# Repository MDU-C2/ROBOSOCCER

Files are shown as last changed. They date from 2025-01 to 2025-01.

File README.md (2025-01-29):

Multi-robot Soccer - RoboCup
=======================

About
-----------------------
Welcome to the DVA490 and DVA474 Project Course, project name Multi-robot Soccer - RoboCup. 
The project is about creating SSL RoboCup (Division B) robots and developing the accompanying software.

Roadmap
-----------------------
Hardware:
- [ ] Hardware mechanical design
- [ ] Hardware 3D design
- [ ] Hardware circuit/electrical design

Software:
- [x] Simulation Interface
- [x] SSL Interface
- [ ] Hardware Interface
- [ ] Communication protocol
- [ ] Raspberry Pi executable (Individual Robot Behaviour)
- [ ] Central computer executable (Collective Robot Behaviour)

Contributors and roles
-----------------------
This project was developed by:
- Mudar Ibrahim: Team leader and software developer
- Carl Larsson: Software lead and software developer
- Viktor Eriksson: Software developer
- Jacob Johansson: Software developer
- Aaiza Aziz Khan: Software developer
- Shruthi Puthiya Kunnon: Software developer
- Emil Åberg: Software developer
- Pontus Svensson: Hardware lead, hardware developer and software developer
- Anton Grusell: Hardware developer
- Johanna Melander: Hardware developer
- Fredrik Westerbom: Hardware developer and software developer

### Contact:
Carl Larsson: cln20001@student.mdu.se

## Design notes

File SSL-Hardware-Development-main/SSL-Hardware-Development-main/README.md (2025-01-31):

# SSL-Hardware-Development

## Overview
Welcome to the SSL Robot Project repository! This project encompasses both hardware and software components essential for building and controlling an SSL robot. Our goal is to create a robust, scalable, and maintainable robot platform.

## Repository Structure
- **3D_Models**: Contains all 3D models related to the robot design.
- **Circuits**: Circuit designs for various robot components.
- **BOM**: Bill of Materials for each component.
- **Software**: Firmware and software for motor control and other functionalities.
- **Design_Documents**: Technical specifications and design decisions.
- **Meeting_Notes**: Documentation of project meetings.
- **Misc**: Miscellaneous files and references.
- **Simulations**: Simulation scripts and models.
- **Documentation**: Comprehensive project documentation and guides.

```bash
/SSL-Robot-Project
├── /3D_Models
│   ├── /CAD_Files            # All CAD files for different robot parts
│   ├── /STL_Files            # STL exports for 3D printing
│   └── /Renderings           # Renders of the 3D models
├── /Circuits
│   ├── /Motor_Control        # Motor circuit design files
│   ├── /Kicker               # Kicker circuit design files
│   ├── /Dribbler             # Dribbler circuit design files
│   └── /Sensor               # Sensor circuit design files
├── /BOM                      # Bill of Materials for different components
├── /Software
│   ├── /Motor_Control
│   │   ├── /Firmware          # Firmware code for motor controllers
│   │   │   ├── /src           # Source code files
│   │   │   ├── /include       # Header files
│   │   │   ├── /tests         # Unit and integration tests
│   │   │   └── README.md      # Firmware-specific documentation
│   │   ├── /Software_Doc      # Documentation related to motor control software
│   │   │   ├── /API_Docs      # API documentation if applicable
│   │   │   └── /User_Guides   # User manuals or setup guides
│   │   ├── /Libraries         # Any libraries or dependencies specific to motor control
│   │   └── /Examples          # Example projects or usage scenarios
│   ├── /Kicker_Control        # Similar structure for kicker control software
│   ├── /Dribbler_Control      # Similar structure for dribbler control software
│   └── /Sensor_Control        # Similar structure for sensor control software
├── /Design_Documents          # Technical specifications, design decisions
├── /Meeting_Notes             # Notes from each project meeting
├── /Misc                      # Any other miscellaneous files
├── /Simulations               # Simulation files or scripts if applicable
├── /Documentation             # General documentation for the project
│   ├── README.md              # Overview of the project
│   ├── CONTRIBUTING.md        # Guidelines for contributing
│   ├── LICENSE.md             # Licensing information
│   └── /Wiki_Links            # Links to relevant wiki pages
└── .gitignore                 # Git ignore file
```

## Getting Started

### Prerequisites
- **Hardware**: Access to the necessary hardware components as listed in the BOM.
- **Software**: Install required software dependencies (refer to [Dependencies](Software/Software_Dependencies.md) documentation).

### Setup Instructions
1. **Clone the Repository**
    ```bash
    git clone git@github.com:DVA490-474-Project-Course/SSL-Hardware-Development.git
    cd SSL-Robot-Project
    ```

2. **Setup Software Environment**
    - Navigate to the software directory:
        ```bash
        cd Software/Motor_Control
        ```
    - Follow the instructions in `README.md` to build and deploy the firmware.

3. **Accessing Documentation**
    - Visit the [Wiki](https://github.com/DVA490-474-Project-Course/SSL-Hardware-Development/wiki) for detailed guides and API documentation.

## Contributing
We welcome contributions! Please read our [CONTRIBUTING.md](Documentation/CONTRIBUTING.md) for guidelines on how to get involved.

## License
This project is licensed under the [MIT License](Documentation/LICENSE).

## Contact
For any questions or support, please open an issue or contact the project maintainers.

Pontus Svensson - psn19003@student.mdu.se

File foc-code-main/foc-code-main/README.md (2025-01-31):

Field Oriented control (FOC)
=======================

DISCLAIMER
-----------------------
This code is DEPRICATED. It is incomplete and its only purpose is for future development.

When using the software provided by STM which supports their MCUs a lot of functions and libraries are generated. We have not been able to exclude the libraries generated that isn't necessary for the code to run. In this repo, the team have elected to only upload the main.c file which is the only file that has been changed by the developers. Later in this **README** there is a step-by-step instruction on what the team did in respective software so that those could generate the files. However, there is no way the team could ensure that even though a future user follows the steps provided in the **README** will generate the same files due to the fact that STM might not support the version the team have used in the future, or if STM elects to generate another code using a different library.

About
-----------------------
This repository contains the code running on the ESC for controlling the wheel motors using FOC.

## Built with
The following tools were used to generate and modify the code for FOC:
- [STM32CubeIDE 1.16.1](https://www.st.com/en/development-tools/stm32cubeide.html)
- [STM32CubeMX 6.12.1](https://www.st.com/en/development-tools/stm32cubemx.html)
- [MC Workbench 6](https://wiki.st.com/stm32mcu/wiki/STM32MotorControl:STM32_MC_Workbench) (Only available for Windows.)

Getting started
-----------------------

### Prerequisites

To retrace the steps the students made during the autumn semester of 2024 the hardware componentes below you will need in addtion to the software listed above. Also, you will need a power source and cables which you can solder onto the inverter and motor.

### Hardware
1. [Nanotec DF45L024048-A](https://www.nanotec.com/eu/en/products/1786-df45l024048-a)
2. [Electronic Speed Controller Discovery kit for drones with STM32G431CB B-G431B-ESC1](https://www.mouser.se/ProductDetail/511-B-G431B-ESC1)

### Installation
1. Clone the repository:
```
git clone https://github.com/DVA490-474-Project-Course/foc_code.git
```
2. Download and install STM32CubeIDE 1.16.1, STM32CubeMX 6.12, STM32 Motor Control Software Development Kit (please see ## Built with)

### Step-by-step configuration
1. In the MC Workbench, create a new project.
    1. Under 'General Info' select
        1. Project name 
        2. Num. Motors: 1 Motor
        3. Driving Algorithm: FOC
        4. Inverter
        5. Please see the image for a visual explanation
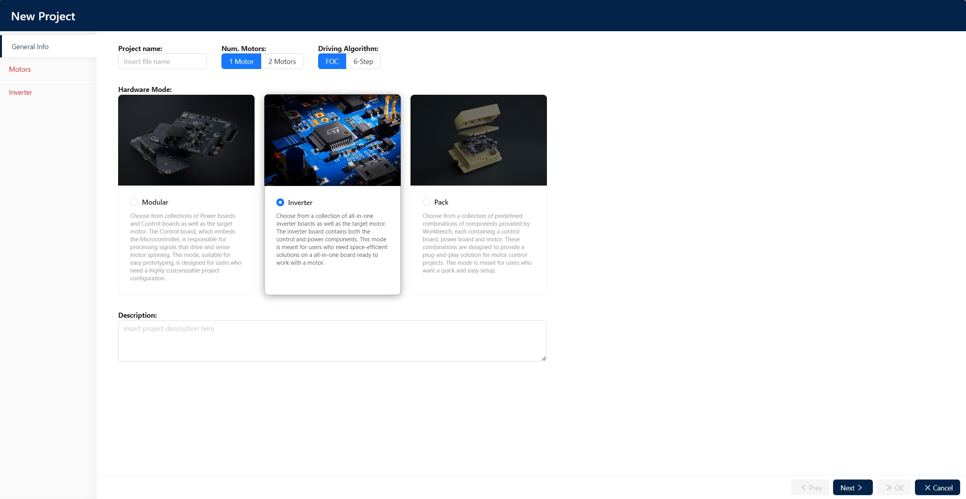
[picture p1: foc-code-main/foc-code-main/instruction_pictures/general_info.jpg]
General Info
        6. 

    2. Under *Motors* select a motor that is similar to the Nanotec DF45L024048-A
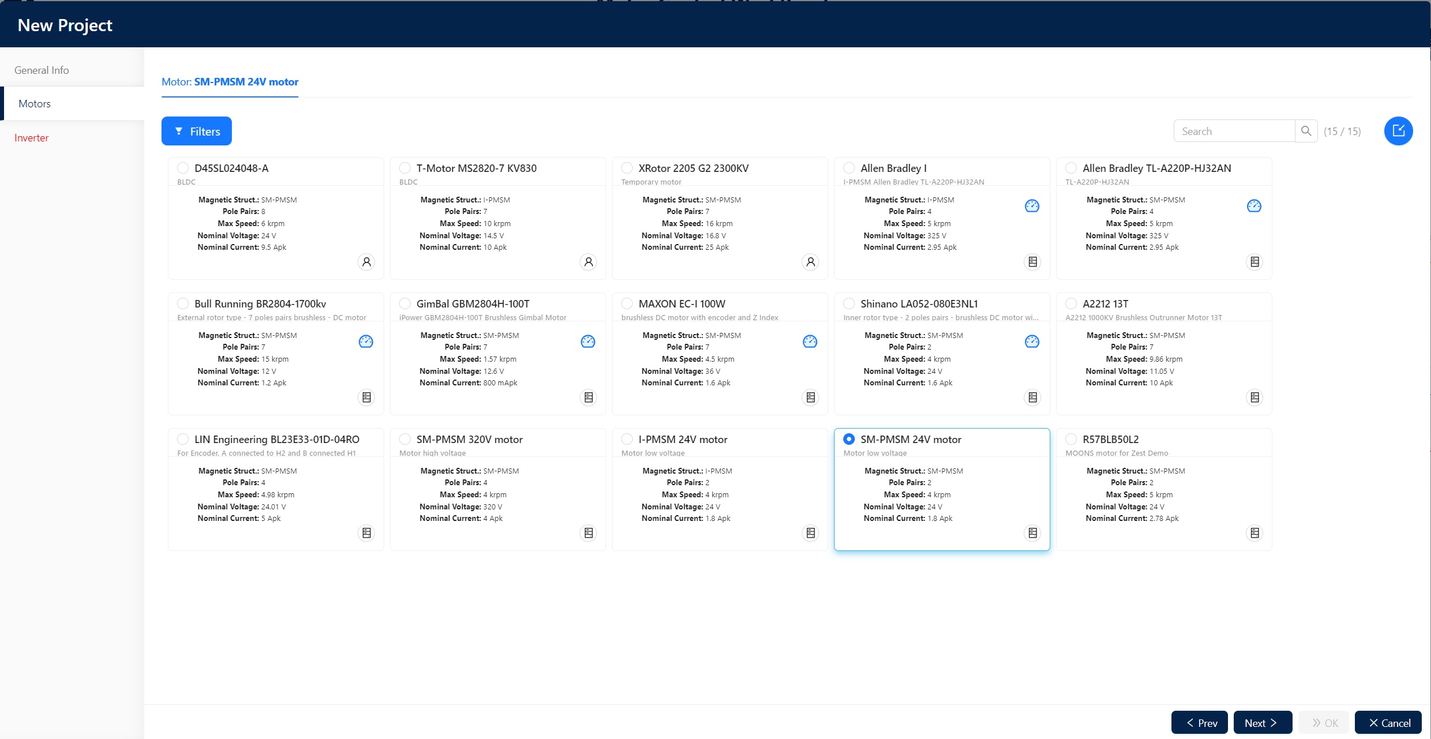
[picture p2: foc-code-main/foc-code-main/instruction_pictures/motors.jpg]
Motors
        1. 
    4. Under the *Inverter* tab select B-G431B-ESC1
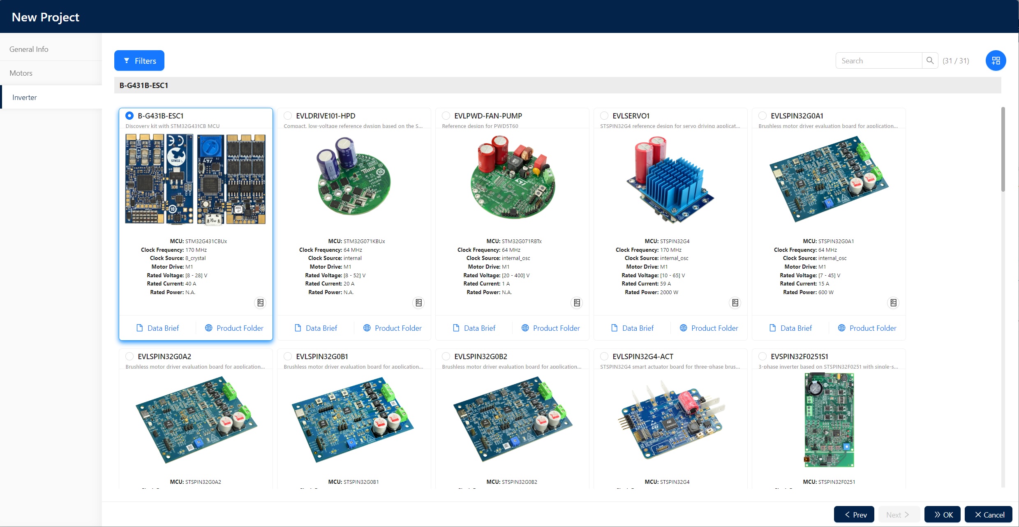
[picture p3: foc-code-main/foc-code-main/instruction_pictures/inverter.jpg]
Inverter
        1. 
    5. Once you've completed all the steps above click ok
2. In the next window called *Project Steps* select the *Application Configuration* tab, check the box for 'Motor Profiler' and click ok
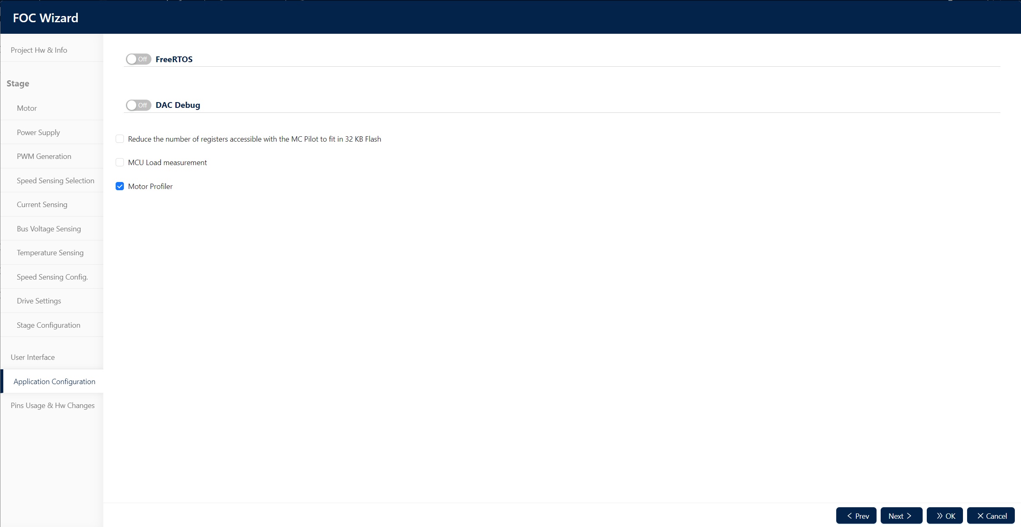
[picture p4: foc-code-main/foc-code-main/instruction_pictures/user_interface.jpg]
Application Configuration
    1. 
3. Click Generate the project - you will be asked to save the project as well.
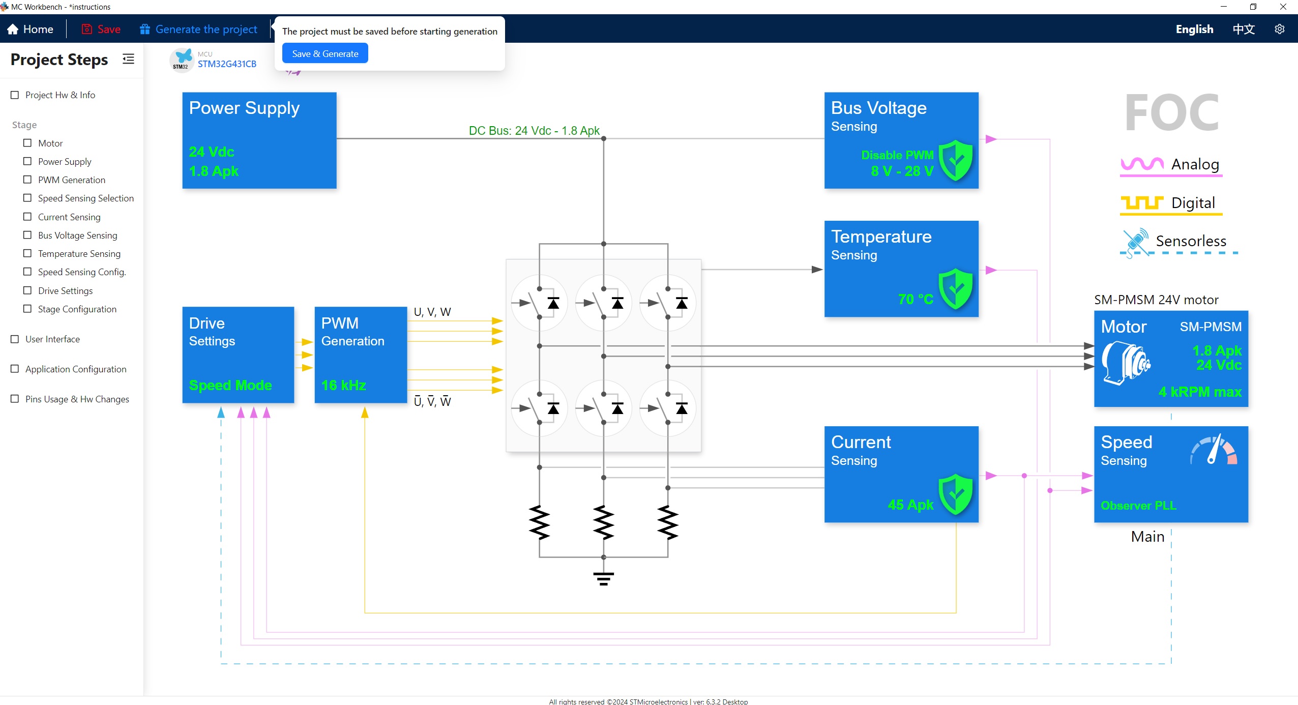
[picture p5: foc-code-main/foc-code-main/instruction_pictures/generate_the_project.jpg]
Generate the project
    1. 
4. A pop-up window will emerge, make sure that all the settings are the same as in the image below (in the extent that it is possible).
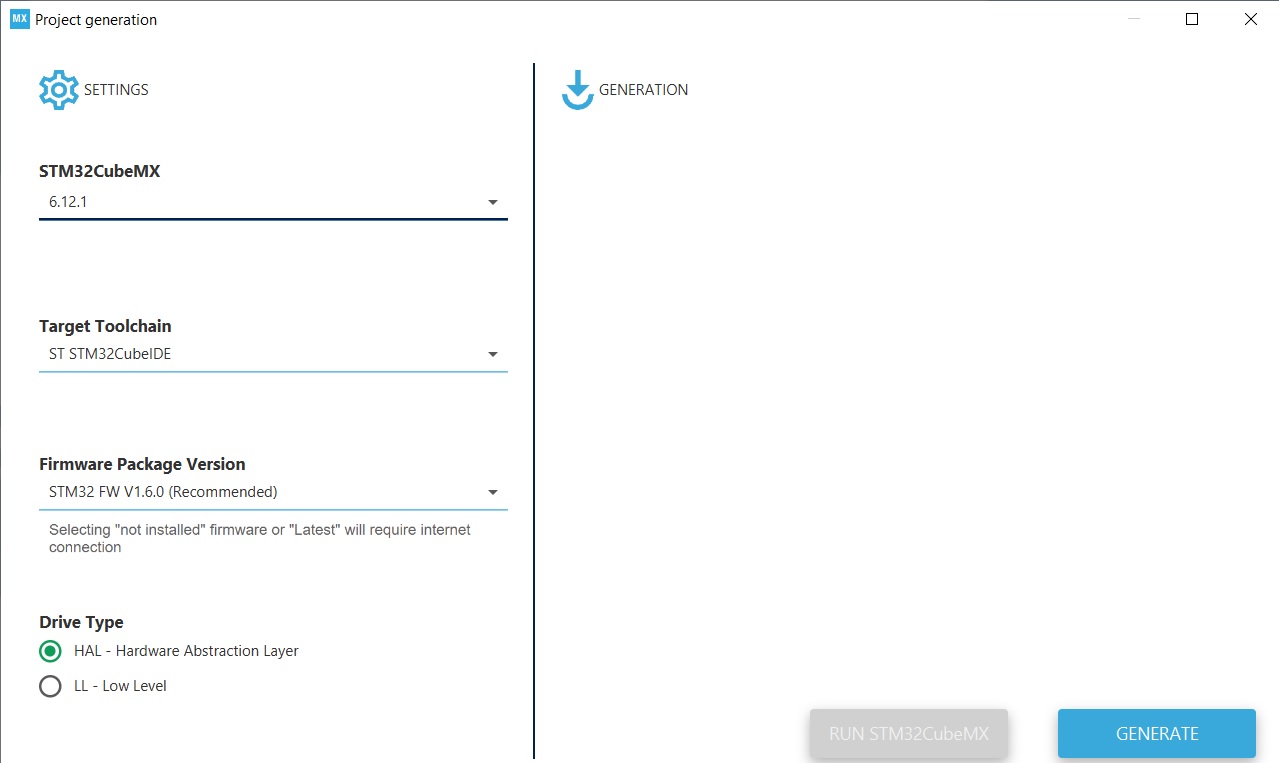
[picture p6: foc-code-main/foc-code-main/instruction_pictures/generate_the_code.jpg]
Generate the code
    1. 
    2. Once it has completed click 'RUN STM32CubeMX'
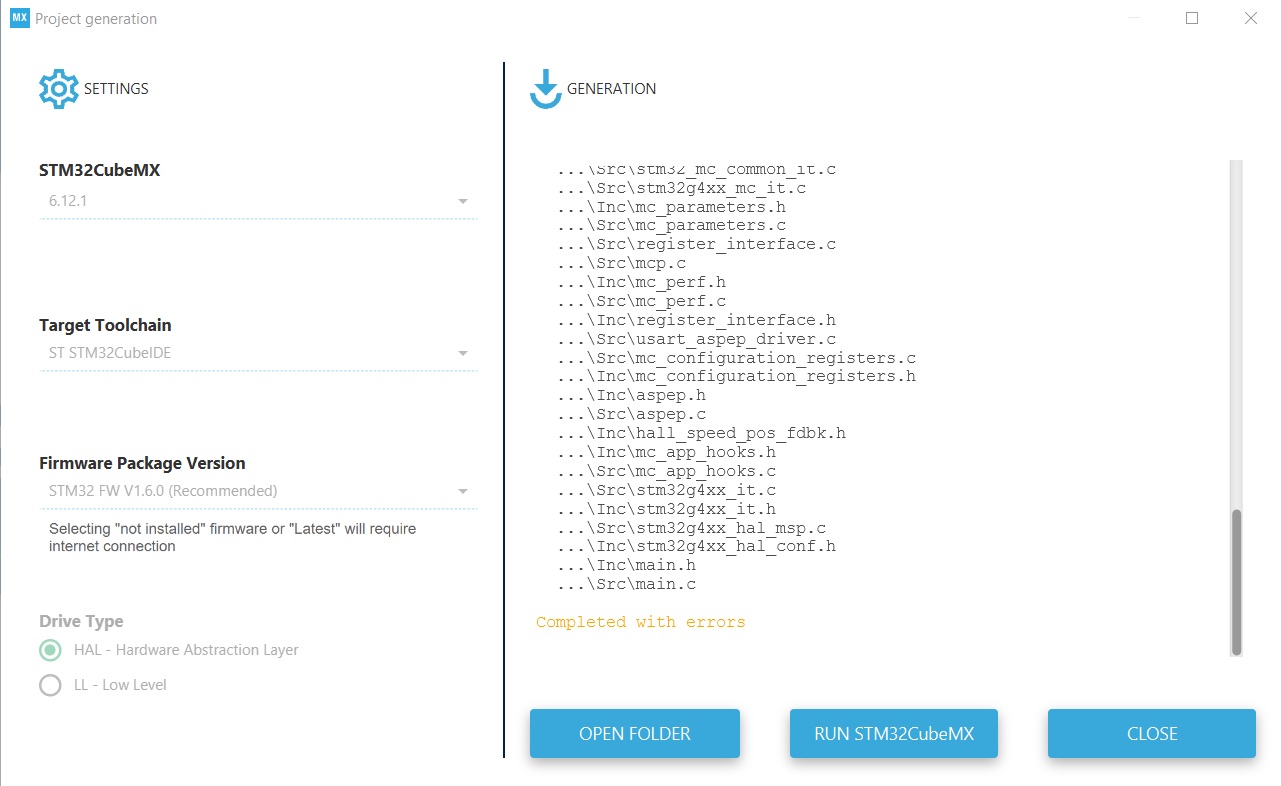
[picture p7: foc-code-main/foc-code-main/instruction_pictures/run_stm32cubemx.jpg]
RUN STM32CubeMX
    3. 
5. Once STM32CubeMX has launched go to the 'Pinout & Configuration' tab and select connectivity. Make sure that the settings for USART2 are the same as in the picture below.
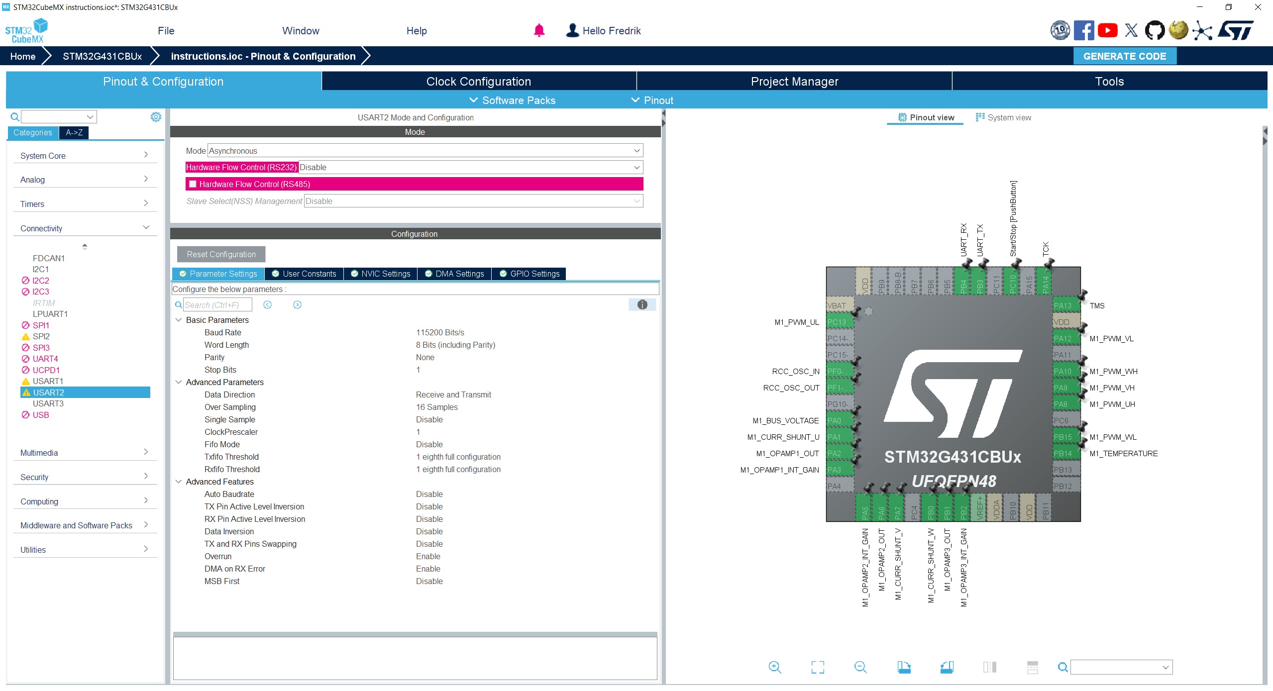
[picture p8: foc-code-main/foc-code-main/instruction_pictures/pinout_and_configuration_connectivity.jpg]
Pinout & Configuration - Connectivity
    1. 
6. Go to 'Project Manager' and in the first tab 'Project' make sure that the option 'Toolchain / IDE' is set to STM32CubeIDE, as seen in the picture (and highlighted with a red arrow).
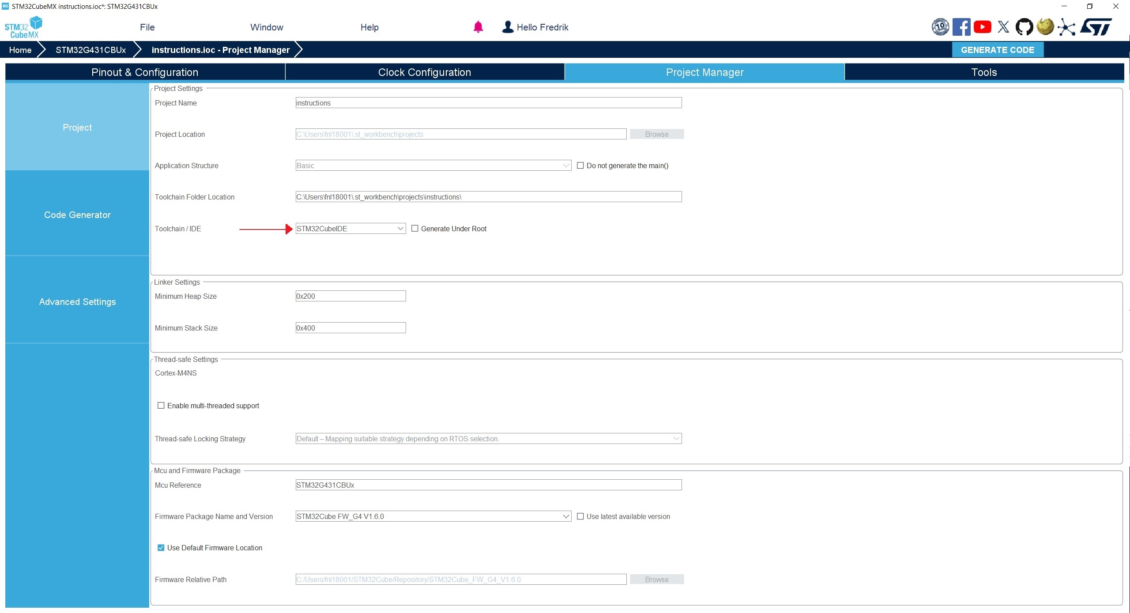
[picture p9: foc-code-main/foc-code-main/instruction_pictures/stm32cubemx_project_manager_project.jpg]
Project Manager - Project
    1. 

-----------------------

Roadmap
-----------------------
- [ ] Establish a connection using UART
- [x] Develop FOC

Design diagrams
-----------------------
Design diagrams/files can be found in the [docs](/docs) directory. Additionally 
they are available on:
- [Hardware Interface](https://www.mermaidchart.com/raw/11c442f5-192c-4ac3-b61e-867a3e2ca6ea?theme=dark&version=v0.1&format=svg)

License
-----------------------
A majority of the code is generated by the STM32CubeIDE and thus distributed under their License (see [liscense](/liscense.pdf)).

Contributors and contact
-----------------------
- Carl Larsson: cln20001@student.mdu.se
- Fredrik Westerbom

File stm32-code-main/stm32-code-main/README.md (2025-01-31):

About
-----------------------
This repository contains the executable code intended to run on the STM32H7 Nucleo-144 board.

### Built with
The stm32-code project is built with the following:

- [STM32CubeIDE](https://www.st.com/en/development-tools/stm32cubeide.html)
- [MicroRos](https://micro.ros.org/)
- [Docker](https://www.docker.com/)

Getting started
-----------------------

### Prerequisites

For STM32CubeIDE installation see: https://www.st.com/en/development-tools/stm32cubeide.html

On Ubuntu and other Debian derivatives, Docker can be installed with:
```
sudo apt install docker
```

In order for microRos dependencies to be downloaded when building, Docker must be
configured to run with root privilige. This can be done with:
```
sudo groupadd docker
sudo usermod -aG docker $USER
```

Log in and out after completing this step in order for group membership to be evaluated.

### Installation
1. Clone the repository and initialize the microROS submodule:
```
git clone https://github.com/DVA490-474-Project-Course/stm32-code.git
cd stm32-code
git submodule update --init --recursive
```
2. Start STM32CubeIDE

3. Log in to your ST account in the IDE if you aren't already logged on.

4. Click 'File>Open Projects from file System...'

5. Click the 'Directory...' button and select the repository folder.

6. Make sure the project is selected in the checklist and click 'Finish'.

7. Generate code by clicking 'Project>Generate Code'. The project is now ready to build.

Usage
-----------------------

In order to upload the program, connect the PC to the USB port CN1  (the one located on
the side of the board which contains the smaller processor, which is the debugger) and
click Run>Run.

Building for the first time may take a few minutes since microROS is downloading its
dependencies to the project.

Roadmap
-----------------------

- [x] Develop Sensor Interface
- [ ] Develop Kicker Interface
- [ ] Develop API to communicate with STM32 on wheel motors
- [ ] Develop API to communicate with STM32 on dribbler
- [x] Implement MicroROS Publishers
- [ ] Implement MicroROS Subscribers

Design diagrams
-----------------------

Design diagrams/files can be found in the [docs](/docs) directory. Additionally
they are available on:
- [Hardware Interface](https://www.mermaidchart.com/raw/11c442f5-192c-4ac3-b61e-867a3e2ca6ea?theme=dark&version=v0.1&format=svg)

License
-----------------------

This repository contains source files from third parties which are distributed
under the license conditions of the respective distrubutors. Source files
developed by the authors of this repository are located in the Core/Src/user-code
directory and is distrubted under the MIT Liscence.

See [MIT Licence](/Core/Src/user-code/LICENSE) for the MIT license.
See [STM32IDE License](/license.pdf) for licence conditions pertaining files accossiated with STM32IDE.
See [VL6180X Driver License](/Drivers/Adafruit_VL6180X/license.txt) for licence conditions pertaining Adafruit's VL6180X driver.
See [VL53L4CD Driver License](/Drivers/VL53L4CD_ULD_Driver/license.pdf) for licence conditions pertaining ST's VL53L4CD driver.
See [WSEN_ISDS Driver License](/Drivers/WSEN_ISDS_2536030320001/license_terms_wsen_sdk.pdf) for licence conditions pertaining Würth Elektronik's WSEN_ISDS driver.

Contributors and contact
-----------------------
- Aaiza Aziz Khan: akn23018@student.mdu.se
- Mudar Ibrahim: mim20004@student.mdu.se
- Shruthi Puthiya Kunnon: spn23001@student.mdu.se
- Emil Åberg: eag24002@student.mdu.se

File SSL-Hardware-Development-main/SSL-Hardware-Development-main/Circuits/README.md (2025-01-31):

# Circuit Designs

This folder contains all circuitry and PCB design for the robot.

See [CONTRIBUTING.md](Documentation/CONTRIBUTING.md#Contributing-to-Hardware) 

## Changes
Update your changes here, include a description, file, name and commit number.

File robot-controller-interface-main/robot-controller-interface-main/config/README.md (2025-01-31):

nav2 custom config files (DEPRICATED)
=======================
This part of the code, meaning setting up a custom nav2 stack and the 
associated config files, is depricated (and does not work). DO NOT USE IT, 
its only purpose is for future development.

The current issue is described in [this Robotics Stack Exchange Question](https://robotics.stackexchange.com/questions/113468/no-map-received-timed-out-waiting-for-transform-from-base-footprint-to-map).

Alternative
=======================
The temporary alternative is to use the default nav2 stack together with SLAM 
Toolbox. To start everything which is necessary to run the individual robot 
behaviour (path planning):
Start SLAM Toolbox (this requires publishing LIDAR values on the /scan topic):
```
ros2 launch slam_toolbox online_async_launch.py
```
Start the nav2 stack (This requires SLAM Toolbox and odometry being published 
on /odom topic):
```
ros2 launch nav2_bringup navigation_launch.py
```

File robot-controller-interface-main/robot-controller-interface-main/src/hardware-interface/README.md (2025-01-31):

Raspberry Pi to STM32 communication code (DEPRICATED)
=======================
This part of the code, meaning the code for Raspberry Pi to STM32 communication 
is in early development, and is depricated. DO NOT USE IT, 
its only purpose is for future development. Hence it has no documentation.

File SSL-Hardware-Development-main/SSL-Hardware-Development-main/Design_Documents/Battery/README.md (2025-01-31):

# What other teams have used
| battery | power board | Links | Team | Weight |
| --- | --- | --- | --- | --- |
| 6S1P 22.2V 150C LiPo 1300 mAh | custom powerboard | [TIGERS Mannheim 2020 paper](https://tdpsearch.com/#/tdp/soccer_smallsize__2020__TIGERs_Mannheim__0?ref=list) | TIGERs Mannheim | ~216 g  |
| 6S1P 22.2V LiPo | custom powerboard | [Roboteam Twente 2022 paper](https://tdpsearch.com/#/tdp/soccer_smallsize__2022__RoboTeam_Twente__0?ref=list) | Roboteam Twente | ~216 g  |
| Li-Po battery, 22.2 V nominal (6S1P), 1300 mAh | not specified | [RoboIME 2024 Paper](https://tdpsearch.com/#/tdp/soccer_smallsize__2024__RoboIME__0?ref=list) | RoboIME | ~240 g  |
| Li-ion,14.8V 4s1p,2600mAh | not specified | [Compilation Error 2024 paper](https://tdpsearch.com/#/tdp/soccer_smallsize__2024__Compilation_Error__0?ref=list) | Compilation error | ~190 g  |
| YPG 22.2V 1500mAh 70C | not specified | [Sysmic Robotics 2020 paper](https://tdpsearch.com/#/tdp/soccer_smallsize__2020__Sysmic_Robotics__0?ref=list) | Sysmic Robotics | ~350 g  |
| LiPo Battery 4S | Custom powerboard | [ITandroids 2020 paper](https://tdpsearch.com/#/tdp/soccer_smallsize__2020__ITAndroids__0?ref=list) | ITandroids | ~565 g  |

As there are no links to the given batteries, the weights are based on similar products found on google.

# requirements
- Correct voltage for processing unit, sensors,  maneuvering motors, dribbling motor and the kicker solenoid.
- The batteries should last for at least 15 minutes of continuous play.
- easy to replace.
- safe to handle.
- Lightweight.
- Correct C rating.

# Limitations
- Size
- Weight
- Capacity

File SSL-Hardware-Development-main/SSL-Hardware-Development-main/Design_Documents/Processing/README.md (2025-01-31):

## Candidates
- [Arduino Due](https://store.arduino.cc/products/arduino-due)
    - Expensive
    - Easy to program
    - No RF

- [STM32 Nucleo](https://estore.st.com/en/products/evaluation-tools/product-evaluation-tools/mcu-mpu-eval-tools/stm32-mcu-mpu-eval-tools/stm32-nucleo-boards/nucleo-f446ze.html)
    - Is a development board, might not have all necessary inputs
    - Cheap

- [Olimex](https://www.olimex.com/Products/ARM/ST/STM32-E407/open-source-hardware)
    - Cheap, supports a lot of communication protocols
    - Open source, a lot of documentation
    - Zephyr build system
    - [ZigBee RF module](https://www.olimex.com/Products/Modules/RF/)

- [STM32L4 Discovery kit IoT](https://estore.st.com/en/products/evaluation-tools/product-evaluation-tools/mcu-mpu-eval-tools/stm32-mcu-mpu-eval-tools/stm32-discovery-kits/b-l475e-iot01a.html)
    - Supports low power RF

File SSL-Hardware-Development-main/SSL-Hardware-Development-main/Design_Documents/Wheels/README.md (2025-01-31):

## Wheels from Participants 2024
- In all the papers reviewed from 2024, 4 omni wheels are consistently used. 
- 3D-printed wheels made from PLA did not hold up. 
- The wheel size depends on the weight of the robot. 
- Bigger wheels can make the robot faster, but the extra weight slows it down by requiring more energy to move.
- More rollers resulted in a smoother motion and more contact with the ground. 
## Team that switched from 3 to 4 wheels
- Some teams initially used 3 wheels but later switched to 4, without giving a specific reason for the change.

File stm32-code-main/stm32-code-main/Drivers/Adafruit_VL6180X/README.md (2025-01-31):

# Adafruit VL6180X Library Documentation

This is a library for the Adafruit VL6180X Time of Flight Distance Ranging Sensor:
  * https://www.adafruit.com/products/3316
 
Check out the links above for our tutorials and wiring diagrams. This chip uses I2C to communicate

Adafruit invests time and resources providing this open source code, please support Adafruit and open-source hardware by purchasing products from Adafruit!

Written by ladyada for Adafruit Industries. BSD license, all text above must be included in any redistribution

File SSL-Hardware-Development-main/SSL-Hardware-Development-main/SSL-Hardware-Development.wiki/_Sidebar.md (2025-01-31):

<!--TODO: Add functional requirements, robot specifications
Add the rest of the components
If the home page gets to long, consider dividing it into their own files and link to them -->
## [Home](https://github.com/DVA490-474-Project-Course/SSL-Hardware-Development/wiki)
## Introduction
- [Requirements](https://github.com/DVA490-474-Project-Course/SSL-Hardware-Development/wiki/Requirements)
- [Functional Requirements](https://github.com/DVA490-474-Project-Course/SSL-Hardware-Development/wiki/Functional_requirements)
- Robot specifications TODO
## System Overview
## Components:
- [Motor Wheel](https://github.com/DVA490-474-Project-Course/SSL-Hardware-Development/wiki/Motor_Wheel)
- [ESC](https://github.com/DVA490-474-Project-Course/SSL-Hardware-Development/wiki/ESC)
- [Microcontroller](https://github.com/DVA490-474-Project-Course/SSL-Hardware-Development/wiki/Microcontroller)
- [Dribbler motor](https://github.com/DVA490-474-Project-Course/SSL-Hardware-Development/wiki/Dribbler_motor)
- **Proximity sensors**
    - [VL6180](https://github.com/DVA490-474-Project-Course/SSL-Hardware-Development/wiki/VL6180)
    - [VL53L4CD](https://github.com/DVA490-474-Project-Course/SSL-Hardware-Development/wiki/VL53L4CD)
    - [SENS0374](https://github.com/DVA490-474-Project-Course/SSL-Hardware-Development/wiki/SENS0374)
    - [APDS-9960](https://github.com/DVA490-474-Project-Course/SSL-Hardware-Development/wiki/APDS-9960)
- [Raspberry Pi](https://github.com/DVA490-474-Project-Course/SSL-Hardware-Development/wiki/Raspberry)
- [Raspberry Pi camera module 3](https://github.com/DVA490-474-Project-Course/SSL-Hardware-Development/wiki/Raspberry_cam)
- [iC-PX2604 + PX01S 26-30](https://github.com/DVA490-474-Project-Course/SSL-Hardware-Development/wiki/Wheel_encoder)
## Schematics & Diagrams
## Assembly Instructions
- [Wheels](https://github.com/DVA490-474-Project-Course/SSL-Hardware-Development/wiki/wheels)
- [Dribbler](https://github.com/DVA490-474-Project-Course/SSL-Hardware-Development/wiki/dribbler)
- [Kicker](https://github.com/DVA490-474-Project-Course/SSL-Hardware-Development/wiki/kicker)

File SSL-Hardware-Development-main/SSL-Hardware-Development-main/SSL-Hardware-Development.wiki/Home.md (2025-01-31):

# Hardware Documentation

## Table of Contents
1. [Introduction](#introduction)
2. [System Overview](#system-overview)
3. [Components](#components)
4. [Schematics & Diagrams](#schematics--diagrams)
5. [Assembly Instructions](#assembly-instructions)

## Introduction
Welcome to the wiki page for the course in DVA490. This years iteration of the project focused on developing an omnidirectional robot. This wiki page will serve as documentation for our robot, the hardware used and how it is assembled streamlining the integration for future improvements of the compoenents. 
The robot consist of 4 omnidirectional wheels, 4 BLDC motors and 1 BLDC motor for the dribbler, a kicker and a mainboard for powering the electronics. 

## System Overview
<!--Describe the system architecture, main features, and working principles.-->
The heart of the robot is the [NUCLEO-H723ZG](https://github.com/DVA490-474-Project-Course/SSL-Hardware-Development/wiki/Microcontroller), it controls the data sampled from the sensors, calculate the kinematics and much more through a middleware called micro-ROS.

<!--## Components-->
<!--See **[BOM](https://github.com/DVA490-474-Project-Course/SSL-Hardware-Development/tree/new_structure/BOM)** for a full list of components.-->
<!--### List of Major Components-->
<!--- **[BLDC Motor](https://github.com/DVA490-474-Project-Course/SSL-Hardware-Development/wiki/Motor_Wheel)**-->
<!--- **[Electronics Speed Controller (ESC)](https://github.com/DVA490-474-Project-Course/SSL-Hardware-Development/wiki/ESC)**-->
  
## Schematics & Diagrams
Include diagrams for electrical circuits, mechanical layout, and connectivity.

## Assembly Instructions
The assembly section describes how to assemble the components. The assembly instructions for the [wheels](https://github.com/DVA490-474-Project-Course/SSL-Hardware-Development/wiki/wheels), [Dribbler](https://github.com/DVA490-474-Project-Course/SSL-Hardware-Development/wiki/dribbler) and [Kicker](https://github.com/DVA490-474-Project-Course/SSL-Hardware-Development/wiki/kicker) can be found in the sidebar.

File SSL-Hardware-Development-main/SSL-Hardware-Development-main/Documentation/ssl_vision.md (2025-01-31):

# Requirements and installation

## Operating system
Ubuntu in the latest LTS version

## Hardware Requirements
SSL-Vision has been tested on x86-compatible computers.

The system supports
- 1394B / FireWire 800
- 1394A / FireWire 400
- Video4Linux
- Matrix-Vision BlueFox2 (USB)
- Gigabit Ethernet (using flycap)
- FLIR USB3 (using Spinnaker SDK) cameras

AVT Stringray F046C firewire cameras have been used at official RoboCup tournaments.

Since 2019, USB 3 FLIR Blackfly S (BFS-U3-51S5C-C) cameras are used.

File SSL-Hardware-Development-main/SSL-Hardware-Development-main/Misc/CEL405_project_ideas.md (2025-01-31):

# CEL405 Project ideas

### 1. **Design and Implementation of an Omni-Directional Motor Control System**

**Objective:** Develop an advanced motor control system for the robot's omni-directional wheels.

- **Analyze complex problems within electronics:**
  - Understand the dynamics of omni-directional movement.
  - Identify the challenges in controlling multiple motors simultaneously.
- **Specify requirements for complex systems:**
  - Define performance metrics like speed, accuracy, and response time.
  - Determine hardware and software requirements.
- **Apply advanced methods:**
  - Implement algorithms like PID control, vector control, or model predictive control.
  - Use simulation tools for system modeling.
- **Propose own solutions:**
  - Optimize motor control for energy efficiency or precision.
- **Present findings:**
  - Prepare a technical report detailing design choices, implementations, and test results.
  - Conduct a seminar presentation with demonstrations.

### 2. **Development of a High-Efficiency Kicker Mechanism**

**Objective:** Create a kicker mechanism that can accurately and powerfully kick a ball.

- **Analyze complex problems:**
  - Study the physics of kicking mechanisms (e.g., solenoid kickers, pneumatic systems).
- **Specify requirements:**
  - Set parameters for force, speed, size constraints, and safety.
- **Apply advanced methods:**
  - Use finite element analysis (FEA) to model mechanical stresses.
  - Implement energy storage solutions like capacitors for quick energy release.
- **Propose solutions:**
  - Innovate on existing designs to improve efficiency or reduce size.
- **Present findings:**
  - Document the design process and testing phases.
  - Share results in a seminar with possible live demonstrations.

### 3. **Sensor Integration and Data Fusion**

**Objective:** Integrate multiple sensors and develop a data fusion algorithm for improved robot perception.

- **Analyze complex problems:**
  - Understand different sensor modalities (e.g., infrared, ultrasonic, encoders).
  - Identify challenges in sensor noise and data synchronization.
- **Specify requirements:**
  - Determine necessary sensor accuracy, range, and update rates.
- **Apply advanced methods:**
  - Develop algorithms for sensor data fusion like Kalman filters.
  - Use signal processing techniques to filter out noise.
- **Propose solutions:**
  - Innovate ways to combine sensor data for better obstacle detection or localization.
- **Present findings:**
  - Provide a comprehensive report with data analysis.
  - Present a seminar with visualizations of sensor data.

### 4. **Design of an Efficient Dribbler Mechanism**

**Objective:** Build a dribbler mechanism that can control the ball effectively during movement.

- **Analyze complex problems:**
  - Explore the mechanics of ball control and surface interactions.
- **Specify requirements:**
  - Define torque, speed, and material requirements for the dribbler.
- **Apply advanced methods:**
  - Use CAD software for mechanical design.
  - Implement control algorithms for dribbler motor speed regulation.
- **Propose solutions:**
  - Experiment with different materials or textures for optimal grip.
- **Present findings:**
  - Document prototypes and testing results.
  - Share insights during a seminar presentation.

### 5. **System Integration and Testing**

**Objective:** Integrate all subsystems (kicker, dribbler, motor control, sensors) and perform comprehensive testing.

- **Analyze complex problems:**
  - Identify integration challenges such as signal interference or power distribution.
- **Specify requirements:**
  - Establish communication protocols between subsystems.
  - Define overall system performance metrics.
- **Apply advanced methods:**
  - Use systems engineering principles.
  - Implement real-time operating systems (RTOS) for task scheduling.
- **Propose solutions:**
  - Develop custom PCBs for efficient layout.
- **Present findings:**
  - Compile a full system report.
  - Demonstrate the fully integrated robot in action during the seminar.

### 6. **Development of Advanced Communication Systems**

**Objective:** Implement a robust wireless communication system between the robot and a base station.

- **Analyze complex problems:**
  - Address issues like latency, bandwidth limitations, and signal interference.
- **Specify requirements:**
  - Set communication range, data rates, and reliability standards.
- **Apply advanced methods:**
  - Utilize communication protocols like Zigbee, Wi-Fi Direct, or custom RF solutions.
  - Implement error-checking and correction algorithms.
- **Propose solutions:**
  - Optimize antenna designs for better reception.
- **Present findings:**
  - Present communication tests and throughput analysis.
  - Demonstrate live communication during the seminar.

### 7. **Power Management and Battery System Design**

**Objective:** Design an efficient power management system to meet all the robot's energy needs.

- **Analyze complex problems:**
  - Calculate total power consumption and identify peak usage times.
- **Specify requirements:**
  - Choose appropriate battery technology (Li-Po, Li-Ion) considering capacity and weight.
- **Apply advanced methods:**
  - Design power distribution boards with voltage regulation.
  - Implement energy-saving modes in software.
- **Propose solutions:**
  - Explore regenerative braking to recover energy.
- **Present findings:**
  - Provide documentation on power efficiency improvements.
  - Share results and battery life tests in the seminar.

### 8. **Software Development for Real-Time Control Systems**

**Objective:** Develop software capable of real-time control and decision-making for the robot.

- **Analyze complex problems:**
  - Tackle challenges in real-time data processing and control loop timing.
- **Specify requirements:**
  - Define software architecture and response time constraints.
- **Apply advanced methods:**
  - Implement real-time operating systems (RTOS) or use microcontroller interrupt systems.
  - Develop algorithms for path planning and obstacle avoidance.
- **Propose solutions:**
  - Optimize code for efficiency and reliability.
- **Present findings:**
  - Document software architecture and algorithms used.
  - Live demonstrations of software capabilities during the seminar.

### 9. **Application of Machine Learning for Enhanced Performance**

**Objective:** Use machine learning to improve robot functions like navigation or object recognition.

- **Analyze complex problems:**
  - Understand the limitations of traditional control systems.
- **Specify requirements:**
  - Determine data requirements for training models.
- **Apply advanced methods:**
  - Implement neural networks or reinforcement learning algorithms.
  - Use simulation environments for training.
- **Propose solutions:**
  - Develop models that adapt to changing environments.
- **Present findings:**
  - Showcase improvements over baseline systems.
  - Present model training and validation results.

### 10. **Technical Documentation and Reporting**

**Objective:** Emphasize the importance of documentation throughout the project lifecycle.

- **Analyze complex problems:**
  - Identify key areas where documentation is critical.
- **Specify requirements:**
  - Establish standards for documentation (e.g., IEEE standards).
- **Apply advanced methods:**
  - Use tools for version control and collaborative writing.
- **Propose solutions:**
  - Develop templates and guidelines for future projects.
- **Present findings:**
  - Submit a comprehensive project report.
  - Reflect on the documentation process during the seminar.

---

Each of these tasks encourages students to:

- **Deepen their knowledge** in specific areas relevant to electronics and robotics.
- **Engage in both theoretical and practical work**, ensuring a well-rounded learning experience.
- **Fulfill the course learning outcomes** by analyzing complex problems, specifying requirements, applying advanced methods, proposing solutions, and effectively communicating their work.

**Implementation Tips:**

- **Form Interdisciplinary Teams:** Encourage collaboration among students with different strengths (e.g., mechanical design, programming, electronics) to simulate real-world engineering teams.
- **Set Milestones:** Break down each task into smaller milestones with deadlines to keep students on track.
- **Provide Resources:** Supply necessary materials and access to workshops, prototyping tools, and software licenses.
- **Regular Feedback:** Schedule weekly or bi-weekly meetings to monitor progress and provide guidance.
- **Assessment Criteria:** Clearly define how each task will be assessed, focusing on both the process and the final deliverables.

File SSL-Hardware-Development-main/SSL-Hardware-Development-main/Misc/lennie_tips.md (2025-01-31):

Hall effekt ström sensor för att mäta inspänningen till varje fas för att kunna räkna ut hastigheten på motorn.
Skapa ett PID system genom att skicka en desired speed till ESP32, mät sedan strömmen ut från ESCn som sedan går in till en arduino som kör PID reglerar strömmen.

Vi kan börja med att skapa ett system, och så länge vi kör samma motorer och ESCs kommer det att fungera för varje motor.

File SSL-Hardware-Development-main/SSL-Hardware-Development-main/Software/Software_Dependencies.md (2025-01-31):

# Dependencies 

## Software tools
### Circuit and PCB design
- [KiCad](https://www.kicad.org/)
### CAD
- [OnShape](https://www.onshape.com/en/) or other .step compatible CAD software.
### Compiling software
- [Cmake](https://cmake.org/)

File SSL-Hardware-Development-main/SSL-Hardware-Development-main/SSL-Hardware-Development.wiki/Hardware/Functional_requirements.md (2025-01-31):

# Functional Requirements
The functional requirements define the end product and what is expected to be delivered for the working product.

1. [ ] The robot must fit within the 180mm diameter, imposed by SSL rules.
2. [ ] The chassis should be lightweight.
3. [ ] Designed with modularity in mind for easy maintenance.
4. [ ] The robot should use four/three-wheel omni-wheels for fast movement in any direction.
5. [ ] Brushless DC motors (BLDC) with high torque to enable fast acceleration.
6. [ ] Electronic Speed Controller (ESC) to control the BLDC motors with feedback for speed and direction control.
7. [ ] The robot must be able to consistently kick the ball.
8. [ ] A dribbler system for ball control.
9. [ ] Sensors to detect the ball relative to the robot.
10. [ ] Wheel encoders and IMUs for feedback on the robots orientation and speed.
11. [ ] Proximity sensors to avoid collisions with other robots.
12. [ ] Battery management system that powers the motors, sensors, and electronics for the duration of the SSL game time.
13. [ ] Power distribution system for stable power delivery to motors, controllers and other components during high loads.
14. [ ] A real-time processing unit capable of processing sensor data, controlling the actuators, and executing commands.

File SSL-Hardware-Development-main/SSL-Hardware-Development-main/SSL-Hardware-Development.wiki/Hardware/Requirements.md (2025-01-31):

## Hardware requirements from the SSL rulebook

### Shape
0.18 meters wide and 0.15 meters high cylinder at any point in time.

### Dribbling
The roller can actively exert spin on the ball is allowed if:
- The ball does not elevate from the ground.
- Other robots must be able to remove the ball.
- 80% of the area of the ball when viewed from above has to be outside the convex hull around the robot.

### Communication
We are allowed to use any wireless communication except for bluetooth.

The wireless communication has to follow legal regulations of the country.

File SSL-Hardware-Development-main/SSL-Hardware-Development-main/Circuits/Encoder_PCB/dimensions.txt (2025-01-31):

Width: 14.7 mm
Height 16.7 mm

14.271 mm Until first corner
Corner is 3.132 mm

Bottom is 9.841 mm

Right corner is 3.436 mm

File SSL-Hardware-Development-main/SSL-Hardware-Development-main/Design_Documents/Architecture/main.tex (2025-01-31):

\documentclass[a4paper,8pt]{article}

% Packages for formatting
\usepackage{geometry}
\usepackage{float}
\usepackage{array}
\usepackage{lipsum}
% \usepackage{cite}
\geometry{margin=0.5in}
% \usepackage{booktabs}
% \usepackage{bookmark}
\usepackage[table]{xcolor}
\usepackage{graphicx}
% \usepackage{tabularx}
\usepackage{longtable}
\usepackage{amsmath}
\usepackage{caption}

\newcommand\IEEEhyperrefsetup{
bookmarks=true,bookmarksnumbered=true,%
colorlinks=true,linkcolor={black},citecolor={black},urlcolor={blue}%
}
% Preferred hyperref setup, Michael Shell
\usepackage[\IEEEhyperrefsetup, pdftex]{hyperref}
\hypersetup{pdfborder=0 0 0}
% \usepackage{tocloft}

\title{Bill of Materials (BOM) Explanation}
\author{ Pontus Svensson / RoboCup }
\date{\today}

\begin{document}

\maketitle

\newpage
\tableofcontents

\newpage

\section{Introduction}

This document provides an explanation of the Bill of Materials (BOM)
used in the project. Each component listed in the BOM is
described in detail, including its purpose and other relevant
specifications.

\section{BOM}

Table~\ref{table:bom} below outlines the components used in this project along
with their purpose and additional information.
\begin{center}
	\begin{longtable}{|p{3cm}|p{3cm}|p{3cm}|p{1cm}|p{3cm}|p{3cm}|}
		\caption{Main components}
    \label{table:bom}
		\\ \hline \rowcolor{gray!50} \textbf{Component} & \textbf{Description} & \textbf{Purpose} & \textbf{\#} & \textbf{á price (price per robot) SEK} & \textbf{Price in USD}\\ \endhead \hline

		% \rowcolor{gray!50} \textbf{Total price for 1 robot} & \textbf{10457.69} \endlastfoot \hline

		\href{https://www.nanotec.com/fileadmin/files/Datenblaetter/BLDC/DF45/DF45L024048-A.pdf?1656012533}{DF45L024048-A}              & Brushless direct current (BLDC) motor with integrated hall sensors for the wheels & Used to spin the wheels of the robot.                                                                                      & 4  & 830.4 (3273.60) & 74.74 (294.6) \\ \hline
		\href{https://www.hobbywing.com/en/products/xrotor3110}{Hobbywing FPV XRotor 3110 900KV}                                        & Brushless DC motor                                                                & High revolutions per minute (RPM) motor used to control the dribbler.                                                      & 1  & 175.20 (175.20) & 15.77 (15.77) \\ \hline
		\href{https://www.mouser.se/datasheet/2/389/b-g431b-esc1-1848063.pdf}{B-G431B-ESC1}                                             & BLDC motor driver                                                                 & Motor driver with embedded $\mu\text{Controller}$ current sensing and hall sensing to form a closed-loop control algorithm & 5  & 208.96 (1044.8) & 18.8 (94.032) \\ \hline
		\href{https://www.st.com/en/evaluation-tools/nucleo-h723zg.html}{NUCLEO-H723ZG}                                                 & $\mu\text{Controller}$                                                            & Computational power and real-time processing capabilities, supports $\mu\text{ROS}$                                        & 1  & 322.58 (322.58) & 29 (29)       \\ \hline
		\href{https://datasheets.raspberrypi.com/rpi4/raspberry-pi-4-datasheet.pdf}{Raspberry Pi 4 Model B/8GB}                         & Single-board computer                                                             & Processing camera input and performing local path planning                                                                 & 1  & 979 (979)       & 88.11 (88.11) \\ \hline
		\href{https://learn.adafruit.com/adafruit-vl53l4cd-time-of-flight-distance-sensor?view=all}{VL53L4CD ToF}                       & Lidar                                                                             & Obstacle detection (Could not find VL53X ToF)                                                                              & 2  & 176.32 (176.32) & 15.87 (15.87) \\ \hline
		\href{https://www.electrokit.com/upload/product/41013/41013634/DM00112632.pdf}{VL6180 TOF}                                      & Lidar                                                                             & Obstacle detection                                                                                                         & 1  & 39.62 (39.62)   & 3.57 (3.57)   \\ \hline
		\href{https://docs.broadcom.com/doc/AV02-4191EN}{APDS-9960}                                                                     & RGB Sensor                                                                        & Ball detection                                                                                                             & 1  & 199 (199)       & 17.91 (17.91) \\ \hline
		\href{https://wiki.dfrobot.com/BNO055_Intelligent_9_Axis_Sensor_Module_SKU_SEN0374}{SENS0374}                                   & 9-Dof IMU                                                                         & Acceleration, Gyroscope, Magnetometer                                                                                      & 1  & 191 (191)       & 17.19 (17.19) \\ \hline
		\href{https://www.elefun.se/p/prod.aspx?v=65193}{6s 1300mAh -120C - GNB HV XT60}                                                & LiPo-battery                                                                      & Used to power the robot                                                                                                    & 1  & 351.20 (351.20) & 31.6 (31.6)   \\ \hline
		\href{https://www.ichaus.de/product/ic-px-series/#documents}{iC-PX2604 + PX01S 26-30}                                           & Wheel encoders                                                                    & Will be used for odometry and determining the RPM                                                                          & 4  & 224.40 (897.60) & 20.2 (80.78)  \\ \hline
		\href{https://www.we-online.com/components/products/datasheet/2536030320001.pdf}{WSEN-ISDS 6 Axis IMU}                          & 6-DoF IMU                                                                         & Will be used for odometry of the robot                                                                                     & 10 & N/A             & N/A           \\ \hline
		\href{https://www.electrokit.com/upload/product/41020/41020240/Camera_Module_3_Product_Brief.pdf}{Raspberry Pi Camera-module 3} & Camera                                                                            & Provide images in front of the robot to detect the ball and obstacles                                                      & 1  & 369 (369)       & 33.21 (33.21) \\ \hline
	\end{longtable}
\end{center}
\section{Reason for component choice}

\subsection{DF45L024048-A}

% SSL robot motor characteristic
During competition a SSL-robot is most of the time accelerating
\cite{francaRob^oCInSmallSize}. Having a motor which can provide
sufficient torque at any given speed is crucial.

% DF45L024048-A introduction
The DF45L024048-A BLDC motors provides a good tradeoff between torque
and RPM, with integrated hall sensors. The sensors detect the position
of the rotor relative to the stator which gives the ability to control
the motors using commutation. The motor controller uses the signals
from the hall sensors to determine the exact timing for switching the
current in the stator windings. This gives a smooth motor operation
while maximizing torque output.

% Other considerations
The size of the motor has to be taken into account. Having to
large footprint on the motors would cause the kicker (solenoid) to not
fit in the chassi. Using a general 5010 sensorless drone motor could
be used as demonstrated by \cite{veeraghanta2024TeamDescription} but
this motor would require a more sophisticated ESC which would take a
lot of time to develop and manufacture. The problem with searching for
5010 drone motors is that most websites does not show the
full torque graph, they primarly show the torque when the motor is
already spinning at $40\%$ throttle and above. Therefore finding a 5010 drone
motor with adequate torque at low speeds is deceptively difficult.

% Provide sources for my claims
Using hall sensors is a common method utilized by several teams and
proven to be a winning concept \cite{ryllExtendedTeamDescription}\cite{abiyevNEUIslandersTeamDescription}\cite{wuCompilationErrorTeam}\cite{francaRob^oCInSmallSize}.

% Dribbler
\subsection{Hobbywing FPV XRotor 3110 900KV}

% Dribbler requirements
The requirements for the dribbler motor is that it can reach high RPM
(around $10\:000\text{ RPM}$). No feedback is implemented for the
dribbler motor, due to the timeframe of the project a control algorithm will not be implemented.

% Motor driver
\subsection{B-G431B-ESC1}

% Sensorless controller hiccups
A sensorless controller requires that the BLDC motor produce a
measurable back electromotive force (EMF) so the controller can
determine the position of the rotor and therefore cannot provide
smooth commutation at start up and low speeds.
\cite{roweInstrumentationControlHigh2012}

% Introduction to B-G431B-ESC1
The chosen electronics speed controller (ESC) has an STSPIN32F0A
system in package chip which has an integrated STM32 processor with
hall sensor decoding logic and current sensing capabilities. This
makes this ESC a good fit with the DF45L024048-A BLDC motor.

% STSPIN32F0A
The STSPIN32F0A chip is a common choice for controlling BLDC motors in
the SSL competitions which has been proven to be reliable and
succesful
\cite{ryllExtendedTeamDescription}\cite{abousaleh2024TeamDescription}.

% FOC
Field-Oriented control (FOC) can be implemented on the B-G431B-ESC1. Guidance and firmware for the B-G431B-ESC1 has been received from Delft Mercurians that will make the process of implementing this streamlined.

% PID system
A PID system can be implemented on the chip to allow for precise
movement and rapid acceleration which is critical to make fast
directions changes.

% Implementation plan of the PID
The B-G431B-ESC1 will receive a desired velocity, to use this within
a PID system the RPM of each motor is required.

% Size and weight
The size and weight of the ESC does also have to be taken in
consideration, the B-G431B-ESC1 has a small footprint with a
relatively low weight $286\text{g}$. With all the components
integrated on one board will make the assembly process easier and
reduce any external components e.g. hall sensing or mosfets. The
programming for the integrated STM32 is done using STM32 Motor Control
Software Development Kit which is a graphical programming environtment
from ST.

\subsection{NUCLEO-H723ZG Microcontroller}

The \text{NUCLEO-H723ZG} is a development board based on the
STM32H723ZG chip, it comes with all necessary peripheral communication
UART, SPI, I2C and CAN. The STM32H723ZG features an ARM Cortex-M7 core
operating at up to 480 MHz, providing good processing power for
handling multiple real-time tasks required in our application.

Additionally, the STM32 series is widely adopted in RoboCup
competitions, including the \textbf{Small Size League (SSL)} \cite{ryllExtendedTeamDescription}\cite{zhaoZJUNlictExtendedTeam}\cite{wuCompilationErrorTeam}.
This widespread use underscores its reliability and effectiveness in
competititions. By using STM32H723ZG chip, previous teams implementations that is open sourced can be used for guidance when developing.

To manage the various tasks and ensure smooth operation of our robot,
the control architecture will be implemeted using \textbf{micro-ROS} in
combination with \textbf{FreeRTOS} on the NUCLEO-H723ZG.

\textbf{FreeRTOS} is a real-time operating system that provides task
scheduling and resource management. Implementing FreeRTOS on the
NUCLEO-H723ZG allows us to handle multiple concurrent tasks
efficiently, such as sensor data processing, motor control, and
communication with other system components.

By using the STM32H723ZG chip future improvements can be made, without having to replace the hardware and potentially the need to re-program/port using another framework.

% \subsubsection{UdeA collaboration}
%
% UdeA will be programming on the ESP32-S3 with FreeRTOS as their framework. Their proposed method for motor control is to use a AS5600 sensor for each motor to measure the RPM and using the ESP32-S3 to create a closed-loop control algorithm.
%
% This will be a similar implementation to our intended control-algorithm. We will use an optical wheel encoder to measure the RPM, and will be used as feedback to create a closed-loop PID algorithm.
%
% From our perspective the programming that is required for this is similar to UdeA. And thus we could still collaborate even though the microcontroller is different.
%
% I have also not found any teams that have used the ESP32 as their main processor, and almost every team uses STM32 based controller or a Raspberry Pi compute module.

\subsection{Raspberry Pi 4 Model B/8GB}

It is important to accurately detect the ball and other robots in a
timely manner, therefore a Raspberry Pi camera will be used, and the input image
will be processed on the Raspberry Pi 4. The Raspberry pi has
been used in the SSL competitions for this purpose
\cite{ommerExtendedTeamDescription}\cite{satoGreenTea2024Team}. A lot of information and open sourced firmware exist.

The Raspberry Pi 4 was also chosen to be able to run the DWA path
planning algorithm, due to the timeframe of this project, implementing
DWA by ourself would require too much time.

% \subsubsection{UdeA considerations}
%
% UdeA has chosen two different components, TOF400C-VL53L1 and VL6180 TOF that is going to be used for obstacle detection and ball detection. Since we are going to run computationally intensive tasks on the Raspberry Pi, replacing it would disrupt a lot of our planning between the software and hardware team.
%
% Our proposed idea is that we can add these components for extra input to allow us to collaborate when developing the software for these components. 

\subsection{VL53L4CD ToF Sensor}

The \textbf{VL53L4CD ToF} (Time-of-Flight) sensor is a laser-based ranging sensor capable of measuring distances with high accuracy. It is used for obstacle detection in the robot, allowing the system to identify obstacles within close proximity. With a range of up to 1300 mm, it is especially suited for detecting obstacles that could interfere with the robot's navigation. The sensor communicates using I2C, which simplifies integration with the existing hardware.

\subsection{VL6180 TOF Sensor}

The \textbf{VL6180 TOF} sensor, also a Time-of-Flight sensor, serves a similar purpose as the VL53L4CD but operates at shorter distances, making it ideal for near-field obstacle detection. It is also chosen for its compact size and I2C communication, which allows it to seamlessly interface with the microcontroller. The shorter range provides additional resolution for objects very close to the robot, further enhancing obstacle detection accuracy.

\subsection{APDS-9960 Sensor}

The \textbf{APDS-9960} sensor is a versatile RGB sensor with integrated IR sensing capabilities. It is primarily used in this project for ball detection, as it can distinguish colors and detect the presence of nearby objects. This feature enables the robot to differentiate the ball from the surroundings based on color and proximity. Communication is handled via I2C, allowing for easy connection to the system’s microcontroller.

\subsection{SENS0374 Sensor}

  The \textbf{SENS0374}, based on the Bosch BNO055 sensor, is a 9-axis absolute orientation sensor module. It integrates a triaxial accelerometer, gyroscope, and geomagnetic sensor with a 32-bit microcontroller, providing orientation data essential for stable navigation and localization. The module includes an onboard fusion algorithm that combines sensor readings to deliver absolute orientation, minimizing drift over time. The SENS0374 communicates via I2C and SPI, making it flexible for integration with the main controller. This sensor will aid in tracking the robots movement, orientation, and any external forces acting upon it, enhancing its responsiveness in dynamic environments.

\subsection{SX1280IMLTRT + SKY66122-11}

To obtain a reliable connection to the team server, the SX1280IMLTRT RF transceiver with the SKY66122-11
front-end-module is used.

This implementation has been proven succesful by several teams \cite{ryllExtendedTeamDescription}\cite{barretoRoboIMEIgnitingInnovation}.

However, to implement this, a basestation is required and due to the time limitation of this project it is not feasible to design and write firmware for our own network protocol, but these components will be added to the mainboard PCB for future iterations. The communication will instead be done using the wifi on the Raspberry Pi 4.

% \subsubsection{UdeA considerations}
%
% I have not yet gotten it confirmed how UdeA has planned to communicate with the server laptop. But from my assumption they will use the WiFi card placed on the ESP32-S3. 
%
% Teams have acknowledged the difficulties with enabling a reliable connection to the team server, when using components like the nRF52 and Raspberry Pis. Teams that did use the ESP32 for WiFi communication also faced a lot of problems \cite{bhatKgpKubs2020Team}.
%
% Therefore we have opted for a different route that has been used by several teams and proven to be reliable\cite{ryllExtendedTeamDescription}.
%
\subsection{iC-PX2604 + PX01S 26-30}

This wheel encoder comes as a complete module which will be easy to
integrate and in combination with the NUCLEO-H723ZG the resolution of
the encoder is increased.

Optical wheel encoders is commonly used by teams competing in the SSL competitions.

% \subsubsection{UdeA considerations}
%
% UdeA has chosen to use the AS5600 magnetic encoder. This setup requires that a magnet is glued to the end of the shaft for every motor. This process also require that the magnet aligns properly and does not come loose during movement and vibrations. We have not gotten more information about how they intended to attach this sensor.
%
% Therefore we would opt for using our optical wheel encoders instead since the integration is done with the wheel assembly and will attach using screws, making the assembly streamlined. Both sensor will be able to provide sensor values that can be used for RPM estimations and odometry.
%
\subsection{WSEN-ISDS 6 Axis IMU}

The IMU chosen is supplied free of charge from Würth
electronics. It communicates using I2C or SPI which both are available
on the NUCLEO-H723ZG.

% \subsubsection{UdeA considerations}
%
% UdeA has chosen to use two different 9-Dof IMUs, however since we got our IMUs free of charge it is smarter to just use those. They did not mention anything about these sensor during our BOM meeting.
% The implementation of the sensors will be similar to some degree both our IMU and BNO055 IMU supports I2C as communication protocol.

\subsection{Raspberry Pi Camera-module 3}

The Raspberry Pi camera-module 3 is chosen because of its seamless
integration with the Raspberry Pi 4.

% \subsection{IR Break Beam Sensor - 5mm LEDs}
%
% The IR Break Beam sensor will be connected using GPIO pins on the
% NUCLEO-H723ZG with a pull-up resistor. To detect if the ball is touching the dribbler roller.

% \subsubsection{UdeA considerations}
%
% UdeA has chosen to use GY-9960-3.3 APDS-9960 RGB sensor. They did not specify how this is going to be used or implemented during our meeting about their BOM.
%
% We have decided not to include this sensor in our desired BOM since it is unclear what the purpose is.

% \subsection{Connectors}
%
% Connectors for the main PCB board will be supplied by Würth
% electronics.
%
% \subsection{Shaft hub with clamping bracket 4mm}
%
% From our research teams have noticed that if the coupling between the
% motorshaft and wheels does not have a good fit, the shaft will start
% to release tiny metal dust which will be collected by the hub of the
% BLDC motor.
%
% Therefore we have chosen to use this clamp to ensure the coupling is
% secure.
%
% \subsection{Bearings}
%
% Bearings used for the roller.
%
% \subsection{Resistors}
%
% Any Passive components required will be supplied by Würth electroncis
% or if we can find it in 326.
%
% \subsection{Capacitors}
%
% Any Passive components required will be supplied by Würth electroncis
% or if we can find it in 326.
%
% \subsection{Voltage regulators}
%
% The voltage regulators will be used to ensure our components reveice
% the correct voltages, 3.3V, 5V, 12V will be integrated on the custom
% PCB.
%
% The voltage regulators was supplied by Würth electronics.
%
% \subsection{Solenoid}
%
A custom made solenoid would be preferred, but due to time a
generic solenoid will be used for starting car engines.
Supplied by MDU.

\subsection{PCB}

As some of our components require a custom PCB, three PCBs will be designed. A mainboard, kicker-board and encoder board, the main board will host
connectors for the battery, motors, sensors, NUCLEO-H723ZG and pin headers for
powering the Raspberry Pi. The mainboard will also host the RF
transceiver, IMU and voltage regulators.

\section{Hardware Architecture}

Figure~\ref{fig:hardware_architecture} depicting the hardware
architecture of the proposed robot.

\begin{figure}[H]
	\begin{center}
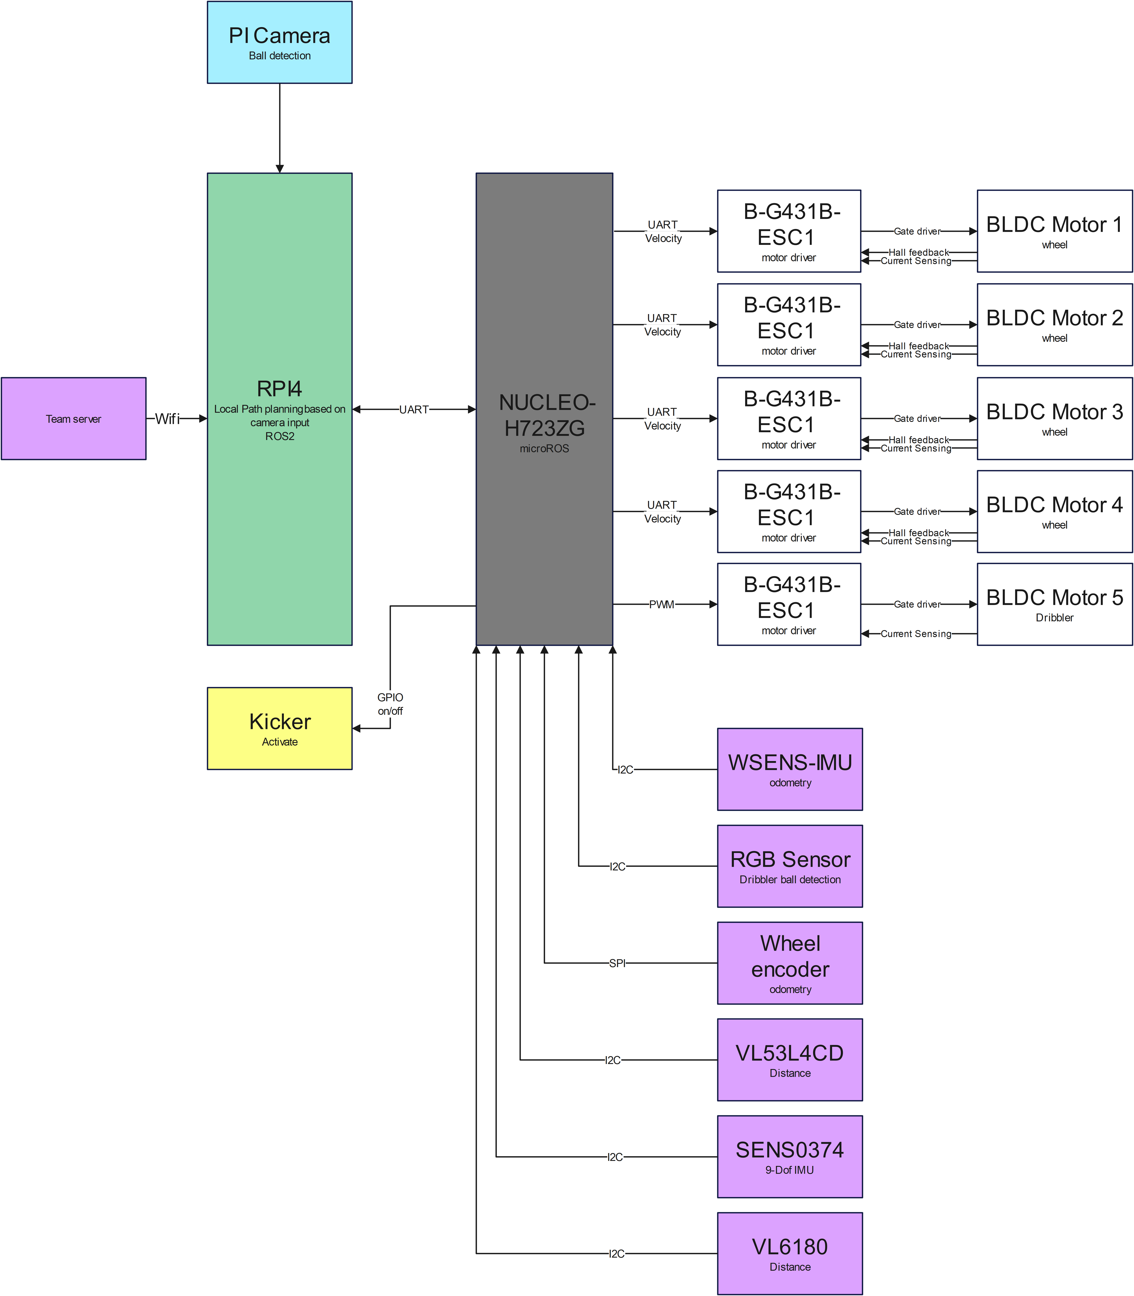
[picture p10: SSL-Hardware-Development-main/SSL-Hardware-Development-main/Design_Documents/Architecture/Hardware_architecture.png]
		
	\end{center}
	\caption{Hardware Architecture}
	\label{fig:hardware_architecture}
\end{figure}

\bibliographystyle{IEEEtran} \bibliography{DVA490_DVA474}
\end{document}

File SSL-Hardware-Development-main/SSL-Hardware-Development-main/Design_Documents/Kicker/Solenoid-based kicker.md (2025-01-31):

- Linear solenoid? 
- Capacitors for power supply
- Controll the force of the kicker (use PWM to controll the capacitors discharge time)
- Some current limiting circuit

## Requirements
- Kicker must generate enough force to kick the ball at high speed
- The capacitor must be large enough to store energy for kicks but small enough to charge quickly
- Solenoid must be durable and capable to withstand frequent, rapid actuation without overheating or lose strength
- The kicker must respond quickly to control signals.
- Minimize energy loss during charging and discharging. 

## Limitations
- Heat management
- Material selection 
- Current rating
- Mechanical wear

## Other teams kicker 

| Team | Solenoid | Kicker charge | Kick speed | |
| --- | --- | --- | --- | --- |
| The A-Team | S-15-75-H (Magnetic Sensor Systems) | | | |
| ZJUNIict | | 4400uF 200V | | |
| ER-Force | | | | |
| Ri-one | | | | |
| UBC Thunderbots | | | | |
| ITAndroids | | | | |
| RoboTeam Twente | Flat solenoid (designen themself) | 1000mikroF 200V | | |
| RoboFEI | | 1000mikroF 200V | | |
| Tigers Mannheim | | 3600mikroF 240V | 8.5 m/s | |
| Robot jacket | | 4000mikroF 250V | 6 m/s | |
| KgpKubs 2017 |  Their own design with description  | | | |
| RFC Cambridge 2016| SOTUH032051. |. |. |. |

  ## Calculations
  - The mass of the golf ball: 0.046kg
  - v=6.5m/s
  - stroke length 0.02m
  - 100V
    
  ## Kinetic Energy: 
  $$E_k = \frac{1}{2} m v^2 $$
  ## Work:
  $$W = F \cdot d = E_k$$
  ### Required force: 
  $$ F = \frac{E_k}{d} = 83.1 N $$
  ## Power Required: 
  $$ P=V \cdot I $$

  ## Capacitor Calculations: 
  - $$E = \frac{1}{2} 0.046 \cdot 6.5^2 = 0.972 J$$
  - $$E = \frac{1}{2} C V^2 J$$
  - $$C = \frac{2 \cdot E}{V^2} = 190.2uF $$

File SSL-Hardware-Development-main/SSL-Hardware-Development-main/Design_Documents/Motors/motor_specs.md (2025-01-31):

### 1. Motor Specifications:
- **Rated Voltage:** 24 V DC
- **Rater Power:** 65 W
- **Rated Speed:** 4840 RPM 
- **Rated Torque:** 0.39 Nm
- **Peak Torque:** 0.56 Nm
- **Torque Constant:** 0.13 Nm/A
- **Rotor Inertia:** 18.1 g*cm²
- **Weight:** 0.15 Kg

### 2. Wheel Specifications:
- **Gear Ratio:** 1:1 (Not usign any) 
- **Wheel Diameter:** 60 mm (Maximum, not final)
- **Traction:** Static friction coefficient 0.7 (Conservative Estimation)

### 3. Robot Mass:
- **Weight Estimation:** 4.5 Kg

### 4. Theoretical Maximum Speed:
- Motor Speed in radian: omega = (4840*2pi)/60 = 506.844 rad/s
- Wheel radius: r = 0.060/2 = 0.030 m
- Linear Velocity: v = omega * r = 15.2 m/s

### 5. Theoretical Maximum Acceleration:
- Total torque: ratet_torque * 4 = 0.39 * 4 = 1.56 Nm
- Force at the wheels: 1.56/0.03 = 52 N
- Acceleration: a = 52 / 4.5 = 11.56 m/s²

### 6. Realistic Speed:
- Velocity: 3 m/s
- Acceleration: 3 m/s²

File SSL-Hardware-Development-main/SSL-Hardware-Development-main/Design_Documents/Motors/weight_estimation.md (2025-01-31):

- Motors: 4*0.15 = 0.6 Kg
- ESC: 5*0.286 = 1.43 Kg
- Battery: 1 * 0.189 Kg
- Dribbler motor: 1 * 0.089 Kg
- Wheel: 4*0.07 = 0.28 Kg
- Raspberry Pi 4: 0.047 Kg
- Nucleo-H723ZG: 0.386 Kg
- Solenoid: 0.190 Kg
- PCB: 0.200 Kg

Total: 3.411 Kg

Deviation: 30%

3.411 * 1.3 = 4.4343 Kg

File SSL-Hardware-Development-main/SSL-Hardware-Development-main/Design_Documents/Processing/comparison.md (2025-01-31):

# Processing Unit Comparison

| Component | ESP32 | STM32-E407 | STM32L496 | STM32H743 | NXP i.MX RT1062 (Teensy 4.0) | Renesas EK-RA6M5 | Nucleo-H743ZI | Nucleo-F429ZI | Notes |
|---|---|---|---|---|---|---|---|---|---|
| **CPU Model** | Xtensa LX6 | ARM Cortex M4 | ARM Cortex-M4 | ARM Cortex-M7 | ARM Cortex-M7 | ARM Cortex-M33 | ARM Cortex-M7 | ARM Cortex-M4 | |
| **Architecture** | 32bit | 32bit | 32bit | 32bit | 32bit | 32bit | 32bit | 32bit | |
| **Clock Speed** | 240 MHz | 168 MHz | 80 MHz | 400 MHz | 600 MHz | 200 MHz | 400 MHz | 180 MHz | |
| **Core Count** | 1 | 1 | 1 | 2 | 1 | 1 | 2 | 1 | |
| **RAM** | N/A | 196 KB | 320 KB | 1 MB | 1 MB | 512 KB | 1 MB | 256 KB | |
| **Cache Size** | 16 KB in RTC | 8 KB | 8 KB | 16 KB | 32 KB | 16 KB | 16 KB | 8 KB | |
| **Wireless Connectivity** | Wi-Fi: 802.11 b/g/n<br>Bluetooth: v4.2 BR/EDR and BLE<br>Need RF module | N/A (Need RF module) | N/A | N/A | N/A | N/A | N/A | N/A | |
| **GPIOs** | 34 | 114 | 114 | 168 | 55 | 168 | 168 | 114 | |
| **ADC** | 12-bit SAR ADC | 3x12-bit 2.4 MSPS | 3x12-bit | 3x16-bit | 12-bit | 2x12-bit | 3x16-bit | 3x12-bit | |
| **DACs** | 2x8-bit | 2x12-bit | 2x12-bit | 2x12-bit | N/A | 2x12-bit | 2x12-bit | 2x12-bit | |
| **SPI** | 4 | 3 | 3 | 6 | 3 | 2 | 6 | 3 | |
| **I2S** | 2 | N/A | 2 | 2 | 1 | N/A | 2 | 2 | |
| **I2C** | 2 | 3 | 3 | 4 | 2 | 2 | 4 | 3 | |
| **UART** | 3 | 6 | 4 | 6 | 8 | 8 | 6 | 6 | |
| **Timers** | 1 | 14 | 10 | 16 | 7 | 16 | 16 | 14 | |
| **CAN bus** | 1 | 2 | 1 | 2 | N/A | 2 | 2 | 2 | |
| **Power** | 3.3V DC | 3.3V - 9V DC | 3.3V DC | 3.3V DC | 3.3V DC | 3.3V DC | 3.3V DC | 3.3V DC | |
| **Price (kr)** | 100:- | 300:- | 350:- | 500:- | 300:- | 600:- | 450:- | 400:- | |
| **micro-ROS Support** | Yes | Yes | Yes | Yes | Yes | Yes | Yes | Yes | |

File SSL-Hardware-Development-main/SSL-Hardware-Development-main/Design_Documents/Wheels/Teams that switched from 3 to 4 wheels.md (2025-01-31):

| Teams | Year (3 wheels) | Year (4 wheels) | Reason for 3 wheels | Reason for the change | Comments |
| --- | --- | --- | --- | --- | --- |
| ER-Force | 2009 | 2010 | No reason | No reason regarding wheels, only regardning motors | |
| Skuba | 2005 | 2009 | No reason | To get more speed and acceleration | |
| Botnia Dragon Knights | 2005 | 2010 | No reason | | |
| RoboPET | | 2010 | No reason | No reason | |
| Bochica | 2011 | | | | Did only compete 2011 |

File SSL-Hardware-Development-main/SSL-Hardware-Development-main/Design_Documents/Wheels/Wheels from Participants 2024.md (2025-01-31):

| Team Name | Number of Wheels | Wheel Type | Wheel Diameter | Number of Rollers | Additional Info |
| --- | --- | --- | --- | --- | --- |
| The A-team | 4 | Swedish (Omni-wheel) | 50mm | 18 8mm rollers | Wheels purchased from GTF robots. |
| The Bots | 4 | Swedish (Omni-wheel) | | | 3D design of the wheels, printed with 85A TPU. |
| UBC Thunderbots | 4 | Omni-wheel | 55mm | 21 rollers | No change from 2020. Material: aluminum |
| RoboIME | 4 | Omni-wheel | 60mm | 24 rollers | |
| Compilation Error | 4 | Omni-wheel | | 16 rollers | |
| Sysmic Robotics | 4 | Omni-wheel | 50mm | 18 rollers | 3D design. No change from 2020 |
| Tritons-RCSC | 4 | Omni-wheel | 50mm | | Purchased from GTF (2023) |
| RoboTeam Twnte | 4 | Omni-wheel | 56mm | | 2017 55mm, 25 rollers, no new information about rollers 2024 |
| KIKS | 4 | Omni-wheel | 56mm | | 56mm 2015, redesigned 2017, no new information about diameter |
| Ri-one | 4 | Omni-wheel | | | |
| SRC | 4 | Omni-wheel | | | |
| NAMeC | 4 | Omni-wheel | | | |
| RoboJackets | 4 | Omni-wheel | 53mm | 20 rollers | |
| OrcaBOT | 4 | Omni-wheel | | | Material: PLA |
| RoboDragons | 4 | Omni-wheel | | | |
| GreenTea | 4 | Omni-wheel | 55mm | | |
| ICRS-FC | 4 | Omni-wheel | 45mm | 20 rollers | |
| Warthog Robotics  | 4 | Omni-wheel | 60mm | | |
| RoboCIn | 4 | Omni-wheel | 45mm | | |
| ITAndroids | 4 | Omni-wheel | | | |
| TurtleRabbit | 4 | Omni-wheel with 2 plates | 67mm | | |
| Luhbots | 4 | | | | |
| ER-Force | 4 | Omni-wheel | 65mm | | |
| Delft Mercurians  | 4 | Omni-wheel | | | 3D design, material: PLA |
| ZJUNlict | 4 | Omni-wheel | 56mm | | |
| Immortals | 4 | Omni-wheel | | 15 rollers | 15 rollers 2018, 18 rollers 2016 with the diameter 61mm. Material 2016 Aluminum |
| TIGERs Mannheim | 4 | Omni-wheel | 62mm | | Material: solid aluminum (2020) |
| RoboFEI | 4 | Omni-wheels | 54mm | | |

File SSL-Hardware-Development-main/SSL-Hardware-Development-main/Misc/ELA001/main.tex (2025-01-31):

\documentclass[a4paper,9pt]{article}
\usepackage{geometry}
\geometry{top=25mm, bottom=25mm, left=25mm, right=25mm}
\usepackage{enumitem}
\usepackage{amsmath}
\usepackage{hyperref}
\usepackage{fancyhdr}
\usepackage{graphicx}
\usepackage{listings}
\usepackage{xcolor}

\title{ELA001}
\author{Examiner: }
\date{\today}

\pagestyle{fancy}
\fancyhf{}
\fancyhead[L]{\leftmark}
\fancyfoot[C]{\thepage}

% Define style for code blocks
\lstset{
    language=C,
    basicstyle=\ttfamily\footnotesize,
    keywordstyle=\color{blue},
    commentstyle=\color{gray},
    stringstyle=\color{red},
    numbers=left,
    numberstyle=\tiny\color{gray},
    breaklines=true,
    frame=single,
    morekeywords={VL53L1_Init, VL53L1_GetDistance, VL53L1_GetRangeStatus, 
                  VL53L1_SetMeasurementTimingBudget, VL53L1_SetRangingMode,
                  VL53L1_SetInterruptThresholds, VL6180_Init, VL6180_GetProximity, 
                  VL6180_GetAmbientLight, VL6180_GetRange, VL6180_SetInterruptConfig,
                  APDS9960_Init, APDS9960_EnableGesture, APDS9960_GetGesture,
                  APDS9960_EnableProximity, APDS9960_GetProximity, APDS9960_EnableAmbientLight,
                  APDS9960_GetAmbientLight, APDS9960_GetColor, APDS9960_SetProximityInterruptThreshold,
                  APDS9960_ClearInterrupt, Motor_Init, Motor_SetSpeed, Motor_GetSpeed, 
                  Motor_SetDirection, Motor_GetDirection, Motor_ReadEncoder, Motor_Stop,
                  BNO055_Init, BNO055_SetOperationMode, BNO055_GetEulerAngles,
                  BNO055_GetAcceleration, BNO055_GetGyro, BNO055_GetMagnetometer,
                  AS5600_Init, AS5600_GetRawAngle, AS5600_GetAngle, AS5600_SetZeroPosition}
}

\begin{document}

\maketitle

\section*{Course Information}
\begin{itemize}[label=--]
	\item \textbf{Course code:} ELA001
	\item \textbf{Subject:} Electronics
	\item \textbf{Credits:} 7.5
	\item \textbf{Main field of study:} Electronics, depth G2F
\end{itemize}

% \section*{Objectives}
% The objective of the course is to allow the student to use the knowledge acquired in electronics to conduct a larger project. The project should deepen the student's theoretical and practical knowledge.

% \section*{Learning Outcomes}
% Upon completion of the course, the student will be able to:
% \begin{enumerate}
% 	\item Conduct a larger project involving the various elements of the project.
% 	\item Orally and in writing, demonstrate understanding of the elements involved.
% 	\item Analyze the limitations of the proposed solution.
% 	\item Present the project both orally and in writing in an informative and constructive manner.
% \end{enumerate}

\section*{Tasks for UdeA}
The following tasks will be completed by University of Antioquia (UdeA):
\begin{enumerate}
	\item \textbf{Hardware Interface for Sensors:}
	      \begin{itemize}
		      \item Design and implement the hardware interface for collecting sensor data.

		            The following are some example API calls the hardware interface should have:
		            \begin{lstlisting}
// VL53L1 Time-of-Flight Sensor
VL53L1_Init();                             // Initialize the sensor
VL53L1_GetDistance();                      // Get distance in mm
VL53L1_GetRangeStatus();                   // Get range status
VL53L1_SetRangingMode(uint8_t mode);       // Set ranging mode
VL53L1_SetInterruptThresholds(uint16_t low, uint16_t high); // Set interrupt thresholds

// VL6180 Proximity and Ambient Light Sensor
VL6180_Init();                             // Initialize the sensor
VL6180_GetProximity();                     // Get proximity value
VL6180_GetRange();                         // Get range distance
VL6180_SetInterruptConfig(uint8_t config); // Configure interrupt settings

// APDS9960 Gesture and Color Sensor
APDS9960_Init();                           // Initialize the sensor
APDS9960_EnableProximity();                // Enable proximity sensing
APDS9960_GetProximity();                   // Get proximity value
APDS9960_GetColor();                       // Get RGBC color data
APDS9960_SetProximityInterruptThreshold(uint8_t low, uint8_t high); // Set proximity interrupt
APDS9960_ClearInterrupt();                 // Clear interrupts
		            \end{lstlisting}

		      \item \textbf{BNO055 Orientation Sensor:}
		            \begin{itemize}
			            \item Implement the interface for the BNO055 sensor to retrieve orientation, acceleration, and other motion-related data.

			                  Example API calls for the BNO055 sensor interface:
			                  \begin{lstlisting}
// BNO055 Sensor Initialization
BNO055_Init();                               // Initialize the BNO055 sensor

// Sensor Configuration
BNO055_SetOperationMode(uint8_t mode);       // Set the operation mode (e.g., IMU, NDOF)

// Sensor Data Retrieval
BNO055_GetQuaternionAngles(float *yaw, float *pitch, float *roll); // Get orientation data (Euler angles)
BNO055_GetAcceleration(float *x, float *y, float *z);         // Get linear acceleration
BNO055_GetGyro(float *gx, float *gy, float *gz);              // Get gyroscope data
BNO055_GetMagnetometer(float *mx, float *my, float *mz);      // Get magnetometer data
			                  \end{lstlisting}
		            \end{itemize}

		      \item \textbf{AS5600 Magnetic Encoder:}
		            \begin{itemize}
			            \item Implement the interface for the AS5600 magnetic encoder to retrieve angular position.

			                  Example API calls for the AS5600 sensor interface:
			                  \begin{lstlisting}
// AS5600 Sensor Initialization
AS5600_Init();                               // Initialize the AS5600 sensor

// Get Raw Angle
AS5600_GetRawAngle();                        // Get the raw angle from the sensor

// Get Adjusted Angle
AS5600_GetAngle();                           // Get the adjusted angle (taking zero-position into account)

// Set Zero Position
AS5600_SetZeroPosition();                    // Set the zero position for angle measurements
			                  \end{lstlisting}
		            \end{itemize}
	      \end{itemize}

	\item \textbf{Hardware Interface for Motors:}
	      \begin{itemize}
		      \item Develop the hardware interface to control the motors for a three-wheeled omni-directional drive system.
		      \item Integrate the interface with the motor drivers.

		            Example API calls for the motor control interface:
		            \begin{lstlisting}
// Motor Initialization
Motor_Init();                               // Initialize the motor controller

// Motor Control
Motor_SetSpeed(uint8_t wheel_id, int speed); // Set the speed of a specific wheel
Motor_GetSpeed(uint8_t wheel_id);            // Get the current speed of the wheel
Motor_SetDirection(uint8_t wheel_id, int dir); // Set the direction (e.g., forward, reverse)
Motor_GetDirection(uint8_t wheel_id);        // Get the current direction of the wheel

// Encoder Readings
Motor_ReadEncoder(uint8_t wheel_id);         // Read the encoder value for a specific wheel

// Stop Motor
Motor_Stop(uint8_t wheel_id);                // Stop the motor
		            \end{lstlisting}
	      \end{itemize}
\end{enumerate}

It is not necessary to implement all of these functions and you can change them as you see fit, but we want an interface for common use of each sensor (i.e. sample data, retrieve range values etc...).

\section*{Embedded System Setup}
Our system will run on an embedded platform using micro-ROS alongside FreeRTOS for real-time task management. micro-ROS will be used for communication and coordination between the different components, while FreeRTOS will handle task scheduling and prioritization. 

\section*{Function Documentation Requirement}
Each function implemented in the project must be properly documented using doxygen. The documentation should include the following:
\begin{itemize}
    \item A clear description of what the function does.
    \item The parameters it accepts (data type and description).
    \item The return values (if applicable) and what they represent.
    \item Any special conditions or limitations for using the function.
    \item Example usage, if necessary, to demonstrate how the function is called and utilized in the code.
\end{itemize}

% Proper documentation will ensure the code is easily understandable, maintainable, and can be reused effectively in the future. This is critical when working in a collaborative environment like this project.

% \section*{Assessment}
% \begin{itemize}[label=--]
% 	\item Written and oral presentation of the project.
% 	\item Analysis of the project solution’s strengths and limitations.
% 	\item Contribution to the group project and collaboration with UdeA.
% 	\item Adherence to proper documentation standards for each function.
% \end{itemize}

\end{document}

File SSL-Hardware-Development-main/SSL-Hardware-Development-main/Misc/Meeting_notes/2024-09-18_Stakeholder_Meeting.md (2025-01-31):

# Stakeholder meeting 2024-09-18

### How can we validate the system? (Software)
- Write out criterias and then develop tests.
- The validation is up to us how we decide to do that, e.g. the stakeholders are okay with our unit tests passing and that our requirements are met.
    - Functional and non-functional requirements.
    - Make sure the functional requirements are defined and set.

### Hardware prototype focus (Hardware)
- We will focus on developing just 1 prototype and making sure it works before building more robots.
    - Once we get our prototype working we can add order components for more robots to save budget in case of hardware failures.
        - It is sufficinet to just build an additional one or two robots to test the team behaviour.
        - This means have a little bit more budget for each robot, but we should still not buy the most expensive stuff.

### If we want to make any hardware changes (Hardware)
- A discussion channel is created in our group on Canvas, here we will write the *reasons* and other arguments as to why this change is necessary. The stakeholders need to be able to provide this information forward to other partners.
- E.g. we want 4 wheels instead of 3. Create a reply in the Hardware discussion channel and provide a clear list of arguments and reason, ideally accompannied by a pdf document which should tell the same thing.

### How detailed should the design files for PRO1 be? (Hardware & Software)
- There is no minimum requirement for how detailed or what type these should be. It is okay with all the sketches and drawings we have made up until now, e.g. block diagrams for the subsystems, CAD models etc.

### Break down the WBS (Hardware & Software)
- Each deliverable should be 8h < x < 40h. 
    - Break down the subsections more, so that each task is clearly defined.

## For the teamleaders
- Meeting with the colombian students, where we can talk about what they want to do. (If their professor is there they wont talk until he says they can talk).
- Suggestion is that the team leaders have a meeting before were we go through what we want the colombian guys to do.

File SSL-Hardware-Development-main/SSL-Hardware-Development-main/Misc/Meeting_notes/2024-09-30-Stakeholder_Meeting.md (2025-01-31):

### General
Det kan vara användbart att få till en kommunikationskanal med UTP för den som arbetar med kicker design.

Dribbler: kolla med Lennie vart kontakterna för motorer osv ska placeras för att minska problem.

Svar på Fredriks fråga i powerpointen:
- Vi kommer behöva en antenn för sensorer

Kolla upp kamerorna som vi ska använda här på C2 för ssl-vision, måste vara exakt samma som dom i Colombia för att vi ska kunna samarbeta.

Vi kan använda en beräkningsmodul t.ex. raspberry pi som tillägg då kan vi köra DWA på den samt lägga till kamera för ball detection.

### WBS feedback

Flera punkter behöver vara tydligare, vad är det exakt som ska levereras. När ett work package är klart så ska vi kunna överlämna ett arbetet till den nästa person.

- t.ex. **Train algorithm** Vad ska tränas och vad är det vi ska kunna efteråt. Analaogy. Jag ska lära mig såga, men vet inte varför.

- Tips är att implementera ett skydd för polvändning, detta är ett genomgående problem från tidigare projekt. Kontaker som kan kopplas åt ett håll, krets som vänder polerna om det skulle kopplas fel. Oring LM7460

**Collaboration**
Bryt ned det mer och skriv in vad dom i UdeA och UTP ska/vill göra.

**Uppgifter**
*UdeA*: Skapa en algorithm för att accelerar snabbt. Vi måste vara tydliga med vad vi vill få ut samt sätta upp några kriterier så att det inte blir för stort scope. T.ex. utvecklad kod, instruktioner på hur den ska köras.

*UTP*: Mer forskande uppgift och fokus på teknisk rapport. T.ex. designa en "chicker", vilka designval har ni gjort och varför, möjligtvis simulering.

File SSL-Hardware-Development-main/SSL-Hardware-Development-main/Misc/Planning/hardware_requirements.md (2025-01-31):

# Suggested areas for hardware
This document contains initial suggestion for areas of focus for the robot. 
Please add more if you have any improvements or suggestions.

A starting point:
- Decide some initial components (not specific).
- Start with a simple block diagram of how we want the components to interact.

## Processing Unit
How should we process everything

Requirements:
- Needs to accept inputs from the sensors, motors, and communication.

Suggestion:
- STM32, ESP32. Depending on the autonomous decision making something more powerful could be necessary.
- If RTOS is necessary the board must support it.

## Communication 

We will need to implement a communication system.
The competiton uses wireless communcication and bluetooth is not allowed.

Suggestion:
- Wi-Fi
- RF modules

## Battery management/Voltage regulation

All electronics wheel need power, circutry for providing power to the different components will be necessary.

Suggestion:
- Li-Po, Li-Ion
- Protection circuitry, prevent overcharge 

## Motor control

What type of motors for the wheels and the roller/kicker.

Suggestion:
- Brushed DC motor, brushless motor.
- PID motor control can be useful
    - Will require some kind of feedback from the motors, e.g. the rpm

## Kicker/Roller

Suggestion from Micke was to use a solenoid and try to make the kicker be able to pass the ball on the ground and chip into the air.

Suggestion:
- Solenoid

## Wheels

Almost all other competitors use some form of swedish wheels. Should we use 3 or 4 wheels etc.

Pros and cons:
- 3 Wheels is lighter and would require less power
- 4 wheels make the robot stable

## Design of kicker, body, wheel house etc.

Initial 3D draft of the robot.

Suggestions:
- Try to keep it light and within the specs for the competition.
- The batteries, kicker, and motors should be easily accessible for replacement.

## Sensors

How are we going to detect the other robots

Suggestion:
- IR sensor
- Ultrasonic sensor
- IMU can be useful for autonomous decision-making

## Cooling

Maybe, idk

## Testing

A test environment will be necessary to ensure that the subsystems works as expected and that we can show that they actually work.

Requirements:
- A standardized way of calibrating the motor speed, solenoid power (if used).
- Some tools for real-time monitoring

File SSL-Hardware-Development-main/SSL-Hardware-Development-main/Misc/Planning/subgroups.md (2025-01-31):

# Physical Robot Hardware Groups

## 1. Powertrain & Electronics
- **Responsibilities**: 
  - Design and implement the power system for the robot, including motors, batteries, and electronic speed controllers (ESCs).
  - Ensure reliable power delivery and efficient energy management.
  - Work on motor control systems and integration with sensors.
- **Key Tasks**:
  - Design and optimize the motor control system.
  - Manage battery selection, power distribution, and charging systems.
  - Integrate ESCs, sensors, and other electronics.

## 2. Mechanical Design & Actuation
- **Responsibilities**:
  - Design the mechanical structure of the robot, focusing on the chassis, actuators, and movement systems (e.g., wheels, kicker).
  - Ensure the robot's agility, durability, and compliance with SSL requirements.
- **Key Tasks**:
  - Develop mechanical systems such as the drivetrain (motors, gears, wheels).
  - Design and implement actuation systems for the kicker, roller, and other movement mechanisms.
  - Ensure that mechanical components are robust and reliable.

## 3. 3D CAD & Body Design
- **Responsibilities**:
  - Create detailed 3D models of the robot's structure and components.
  - Focus on optimizing the robot's size, weight, and overall design to meet RoboCup SSL regulations.
- **Key Tasks**:
  - Develop 3D CAD models for the robot body, including the chassis and outer casing.
  - Collaborate with the mechanical group to ensure designs are manufacturable.
  - Design parts for 3D printing.

## 4. Sensors & Embedded Systems
- **Responsibilities**:
  - Integrate sensors (e.g., cameras, distance sensors) and develop embedded systems for real-time data processing.
  - Focus on the interaction between hardware components and real-world data (e.g., ball tracking, robot positioning).
- **Key Tasks**:
  - Select and integrate sensors into the robot for object detection, localization, and feedback.
  - Develop firmware and embedded systems for real-time sensor processing.
  - Ensure smooth communication between sensors and the robot's main control systems.

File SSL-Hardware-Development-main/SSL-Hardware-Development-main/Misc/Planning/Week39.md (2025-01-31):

# Week 39

### Powertrain & Electronics

- Create a schematic for the whole system (could be made in KiCad, as a blockdiagram). Try to include as much information as possible, i.e. power estimtes, voltage estimates etc.
    - Check so that everything is compatible and if we are required to do some changes.

### Sensor & Embedded system

- Decide on which sensors we want to use if that is not done already.
    - Create initial sensor schematics, ideally it would be done using KiCad but blockdiagram is okay, try to include as much information as possible e.g. voltages and power consumption.
- Research ways to sample the data from these sensors. Initial idea is to use FreeRTOS + micro-ROS on the ESP32.
    - There is no need to program for this task, we want to find out information about efficient/easy ways this could be done.

### CAD

- If the omni-wheels design is done we could print a prototype to see how it looks.
- When we have decided our main components, such as batteries, sensors, motors. Try to modify the base model and fit these components.
- If we have time start looking at the dribbler mechanism, i.e. how to mount the motor, we would need a base design.

### Kicker

- Create a schematic for the kicker, ideally this would be a circuit but can also be a quick sketch using blockdiagrams. Try to include as much details as possible, e.g. current draw, voltage requirements. 
    - A description of how it works and how we intend to use it. E.g. we will need to charge this capacitor and then describe the trigger mechanism.

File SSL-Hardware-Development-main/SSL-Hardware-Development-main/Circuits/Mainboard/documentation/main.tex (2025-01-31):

\documentclass{standalone}
\usepackage{tikz}
\usetikzlibrary{circuits.ee.IEC}

\begin{document}

\begin{tikzpicture}[circuit ee IEC, x=3cm, y=2cm, semithick,
                    every info/.style={font=\footnotesize},
                    small circuit symbols,
                    set resistor graphic=var resistor IEC graphic,
                    set diode graphic=var diode IEC graphic,
                    set make contact graphic= var make contact IEC graphic]

  % Define contacts in a loop for easier modification
  \foreach \contact/\y in {1/1, 2/2, 3/3.5, 4/4.5, 5/5.5} {
    \node [contact] (left contact \contact) at (0,\y) {};
    \node [contact] (right contact \contact) at (1,\y) {};
  }

  % Vertical connections
  \draw (right contact 1) -- (right contact 2) -- (right contact 3)
        -- (right contact 4) -- (right contact 5);

  % Circuit components between contacts
  % First row
  \draw (left contact 1) to [diode] ++(down:1)
                         to [voltage source={near start, direction info={volt=3}},
                             resistor={near end, ohm=3}] ++(right:1)
                         to (right contact 1);
  \draw (left contact 1) to [resistor={ohm=4}] (right contact 1);

  % Second row
  \draw (left contact 1) to [resistor={ohm=3}] (left contact 2);
  \draw (left contact 2) to [voltage source={near start, direction info={<-, volt=8}},
                             resistor={ohm=2, near end}] (right contact 2);

  % Third row with switch
  \draw (left contact 2) to [resistor={near start, ohm=1},
                             make contact={near end, info'={[red]$S_1$}}]
                         (left contact 3);
  \draw (left contact 3) to [current direction'={near start, info=$\iota$},
                             resistor={near end, info={$R=4\Omega$}}]
                         (right contact 3);

  % Fourth row
  \draw (left contact 4) to [voltage source={near start, direction info={<-, volt=8}},
                             resistor={ohm=2, near end}] (right contact 4);
  \draw (left contact 3) to [resistor={ohm=1}] (left contact 4);

  % Fifth row
  \draw (left contact 4) to [resistor={ohm=3}] (left contact 5);
  \draw (left contact 5) to [resistor={ohm=4}] (right contact 5);

  % Final row with upward components
  \draw (left contact 5) to [diode] ++(up:1)
                         to [voltage source={near start, direction info={volt=3}},
                             resistor={near end, ohm=3}] ++(right:1)
                         to (right contact 5);

\end{tikzpicture}

\end{document}

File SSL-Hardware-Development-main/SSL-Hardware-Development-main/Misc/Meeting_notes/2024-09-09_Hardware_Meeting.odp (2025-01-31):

## HW Meeting 2024-09-09

## Intro

- Har alla en ungefärlig idé om hur roboten ska byggas?
  - Komponenter, struktur etc

## Areas for hardware

- Initial idé om indelning för hårdvara där vi kan läsa in oss djupare för att hitta bra stöd från litteraturen och kan gör ett utbildat val för respektive komponent.

## Processing Unit

- Varje robot kommer behöva sin egna processor för att kunna köra AI, kommunicera genom RF/ROS2.
- Input från sensorer
  - En ADC kan kopplas innan ifall Raspberry pi används. T.ex. Pico eller extern ADC.
- Sammarbete med Software (SW)
- Programmering med ROS2/C++

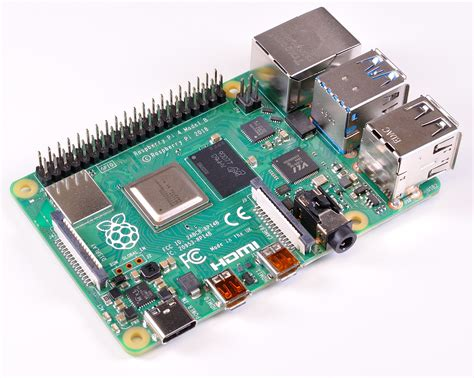
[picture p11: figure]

## Communication

- Robotarn måste kunna kommunicera med varandra och med en extern datorn.
- Hur ska denna kommunikation se ut, vilken form etc.
  - E.g. Radio frequency (RF)
  - Bluetooth är ej tillåtet.
  - Wi-Fi

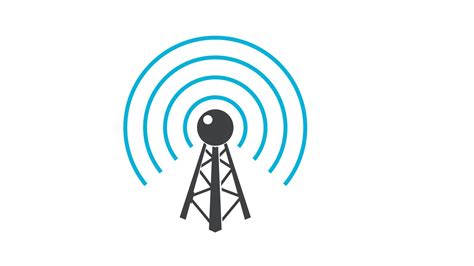
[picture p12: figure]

## Battery management

- All the components will require power
- This group should create protection circuitry for the batteries, provide the correct voltage for the other components
  - Processing unit might require 5V and motor 12V
- Electrical design
  - Multisim or Eagle CAD can be used

## Motor control

- Decide which type of motors that should be used
  - Roller
  - Wheels
- Motor controller such as H-bridges
  - Can be designed or purchased as is depending on motor
- Electrical engineering

## Kicker

- The kicker should most probably be a solenoid, and a electric schematic will be necessary for this.
- Decide which solenoid to be used
- 3D design of the kicker
  - Ideally it should be able to pass and chip the ball
- Electrical engineering
- CAD

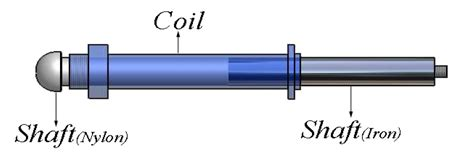
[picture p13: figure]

## Wheels

- Decide what type of wheels we should use and how many wheels.
- Physics

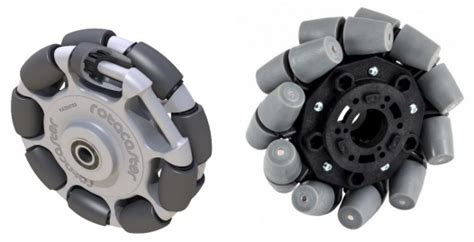
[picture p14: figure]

## 3D design of the robot body

- Initial 3D design of the robot
- CAD

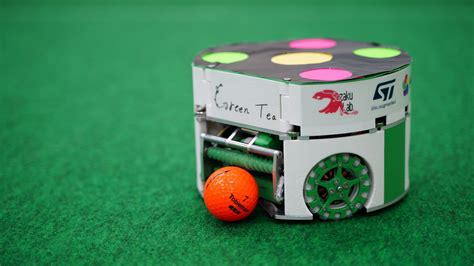
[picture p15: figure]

## Sensors

- Decide what type of sensor we should use for detecting other robots, position of the robot etc
  - IMU
  - IR
  - Ultrasonic
- Sensor knowledge

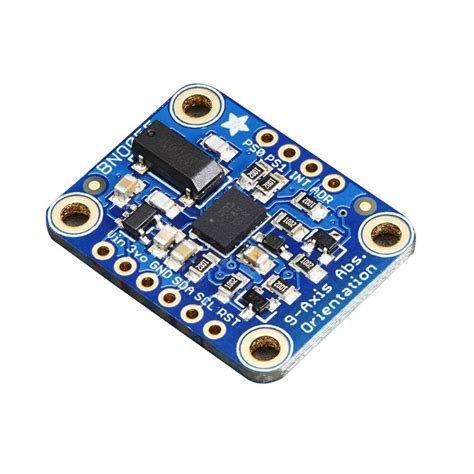
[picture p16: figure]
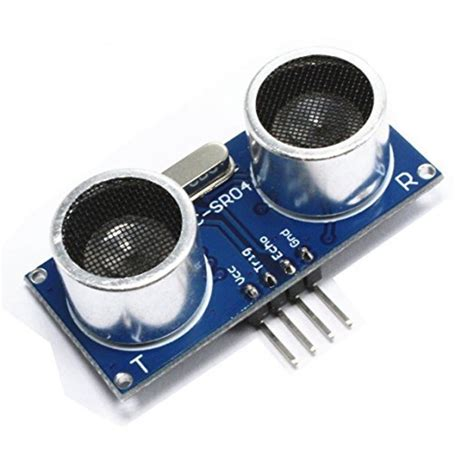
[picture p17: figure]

## Develop a testing environment

- We will need a standardized way to calibrate the robot, a way to validate that the robot behaves as we say it does and that the stakeholders requirements are met
  - Real-time monitoring tools
    - MyDAQ
    - LabView

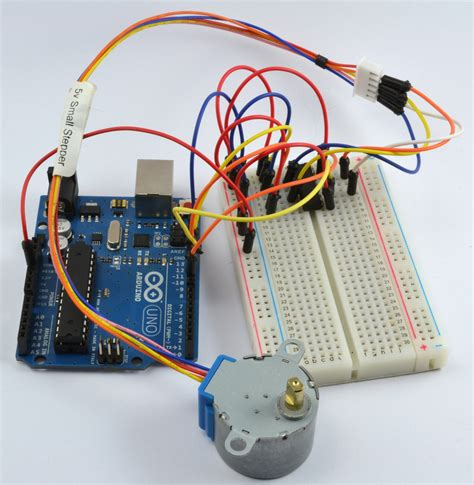
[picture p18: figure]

## Documentation

- Each component used should be described in its own section on the hardware page WIKI
- I will add more information about how this should be done

## Additional

- Additional training to access the battery cabinet
  - 2024-09-16 (1 week from now)
- PRO1 – 2024-09-27
  - 18 Days (2 weeks)
- Develop our plan for the hardware (Ideally a draft at the end of the week)
  - Decide which components to use
  - Cost
- I will create more detailed instructions for each group and add more requirements

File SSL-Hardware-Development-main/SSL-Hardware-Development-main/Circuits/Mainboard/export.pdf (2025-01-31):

export

Position | Name | Type | Signal | Label | Connected
1 PE2 | | I/O | USART10_RX | M4_RX
2 PE3 | | I/O | USART10_TX | M4_TX
3 PE4 | | I/O
4 PE5 | | I/O | TIM15_CH1 | M2_PWM
5 PE6 | | I/O
6 VBAT | | Power
7 PC13 | | Input | GPIO_Input | B1 (Blue_User_Button)
8 PC14-OSC32_IN | | I/O | RCC_OSC32_IN
9 PC15-OSC32_OUT | | I/O | RCC_OSC32_OUT
10 PF0 | | I/O | I2C2_SDA | VL53L4CD_SDA
11 PF1 | | I/O | I2C2_SCL | VL53L4CD_SCL
12 PF2 | | Output | GPIO_Output | VL53L4CD_SHUT
13 PF3 | | Output | GPIO_Output | VL53L4CD_INT
14 PF4 | | I/O
15 PF5 | | I/O
16 VSS | | Power
17 VDD | | Power
18 PF6 | | I/O | TIM23_CH1 | M3_PWM
19 PF7 | | I/O
20 PF8 | | I/O
21 PF9 | | I/O
22 PF10 | | I/O
23 PH0-OSC_IN | | I/O | RCC_OSC_IN | MCO
24 PH1-OSC_OUT | | I/O | RCC_OSC_OUT
25 NRST | | Reset
26 PC0 | | I/O
27 PC1 | | I/O | ETH_MDC | RMII_MDC
28 PC2_C | | I/O | SPI2_MISO | RF_MISO
29 PC3_C | | I/O | SPI2_MOSI | RF_MOSI
30 VDD | | Power
31 VSSA | | Power
32 VREF+ | | MonoIO
33 VDDA | | Power
34 PA0 | | I/O | TIM5_CH1 | M1_PWM
35 PA1 | | I/O | TIM2_CH2 | M1_Encoder_B
36 PA2 | | I/O | USART2_TX | M2_TX
37 PA3 | | I/O | USART2_RX | M2_RX
38 VSS | | Power
39 VDD | | Power
40 PA4 | | Output | GPIO_Output | WSENS_CS
41 PA5 | | I/O | SPI1_SCK | WSENS_SCL
42 PA6 | | I/O | SPI1_MISO | WSENS_SAO
43 PA7 | | I/O | ETH_CRS_DV | RMII_CRS_DV
44 PC4 | | I/O | ETH_RXD0 | RMII_RXD0
45 PC5 | | I/O | ETH_RXD1 | RMII_RXD1
46 PB0 | | Output | GPIO_Output | LED_GREEN
47 PB1 | | I/O
48 PB2 | | I/O

49 PF11 | I/O | TIM24_CH1 | M4_PWM
50 PF12 | I/O
51 VSS | Power
52 VDD | Power
53 PF13 | I/O
54 PF14 | I/O | I2C4_SCL | ADPS-9960_SCL
55 PF15 | I/O | I2C4_SDA | ADPS-9960_SDA
56 PG0 | I/O
57 PG1 | I/O
58 PE7 | I/O
59 PE8 | I/O
60 PE9 | I/O
61 VSS | Power
62 VDD | Power
63 PE10 | I/O
64 PE11 | I/O
65 PE12 | I/O
66 PE13 | I/O
67 PE14 | I/O
68 PE15 | Output | GPIO_Output | RF_CS
69 PB10 | I/O | SPI2_SCK | RF_SCK
70 PB11 | I/O
71 VCAP | Power
72 VDD | Power
73 PB12 | I/O | UART5_RX | Rpi_RX
74 PB13 | I/O | ETH_TXD1 | RMII_TXD1
75 PB14 | I/O | TIM12_CH1 | M5_PWM
76 PB15 | I/O | USART1_RX | M1_RX
77 PD8 | I/O | USART3_TX | STLK_VCP_RX
78 PD9 | I/O | USART3_RX | STLK_VCP_TX
79 PD10 | Output | GPIO_Output
80 PD11 | I/O
81 PD12 | I/O | TIM4_CH1 | M3_Encoder_A
82 PD13 | Output | GPIO_Output | SEN0374_INT
83 VSS | Power
84 VDD | Power
85 PD14 | Output | GPIO_Output | SEN0374_Boot
86 PD15 | Output | GPIO_Output | SEN0374_PS1
87 PG2 | Output | GPIO_Output | SEN0374_PS2
88 PG3 | Output | GPIO_Output | SEN0374_BL-IND
89 PG4 | Output | GPIO_Output | SEN0374_RST
90 PG5 | Output | GPIO_Output
91 PG6 | Output | GPIO_Output | ADPS-9960_INT
92 PG7 | I/O | GPIO_EXTI7 | USB_FS_OVCR
93 PG8 | Output | GPIO_Output | VL6180_IO1
94 VSS | Power
95 VDD33USB | Power
96 PC6 | I/O | TIM8_CH1 | M4_Encoder_A
97 PC7 | I/O | TIM8_CH2 | M4_Encoder_B

98 PC8 | Output | GPIO_Output | VL6180_IO0
99 PC9 | I/O | I2C3_SDA | VL6180_SDA
100 PA8 | I/O | I2C3_SCL | VL6180_SCL
101 PA9 | I/O | USB_OTG_HS_VBUS | USB_FS_VBUS
102 PA10 | I/O | USB_OTG_HS_ID | USB_FS_ID
103 PA11 | I/O | USB_OTG_HS_DM | USB_FS_DM
104 PA12 | I/O | USB_OTG_HS_DP | USB_FS_DP
105 PA13(JTMS/SWDIO) | I/O | DEBUG_JTMS-SWDIO | SWDIO
106 VCAP | Power
107 VSS | Power
108 VDD | Power
109 PA14(JTCK/SWCLK) | I/O | DEBUG_JTCK-SWCLK | SWCLK
110 PA15(JTDI) | I/O | TIM2_CH1 | M1_Encoder_A
111 PC10 | I/O | UART4_TX | M5_TX
112 PC11 | I/O | UART4_RX | M5_RX
113 PC12 | I/O | UART5_TX | Rpi_TX
114 PD0 | I/O
115 PD1 | I/O
116 PD2 | I/O
117 PD3 | I/O
118 PD4 | I/O
119 PD5 | I/O
120 VSS | Power
121 VDD | Power
122 PD6 | I/O
123 PD7 | I/O | SPI1_MOSI | WSENS_SDA
124 PG9 | I/O | USART6_RX | M3_RX
125 PG10 | I/O
126 PG11 | I/O | ETH_TX_EN | RMII_TX_EN
127 PG12 | I/O
128 PG13 | I/O | ETH_TXD0 | RMII_TXD0
129 PG14 | I/O | USART6_TX | M3_TX
130 VSS | Power
131 VDD | Power
132 PG15 | I/O
133 PB3(JTDO/TRACESWO) | I/O | DEBUG_JTDO-SWO | SWO
134 PB4(NJTRST) | I/O | TIM3_CH1 | M2_Encoder_A
135 PB5 | I/O | TIM3_CH2 | M2_Encoder_B
136 PB6 | I/O | USART1_TX | M1_TX
137 PB7 | I/O | TIM4_CH2 | M3_Encoder_B
138 BOOT0 | Boot
139 PB8 | I/O | I2C1_SCL | SEN0374_SCL
140 PB9 | I/O | I2C1_SDA | SEN0374_SDA
141 PE0 | I/O
142 PE1 | Output | GPIO_Output | LED_YELLOW
143 PDR_ON | Power
144 VDD | Power

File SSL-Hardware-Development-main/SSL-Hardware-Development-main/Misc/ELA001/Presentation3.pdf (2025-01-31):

2024-11-13

# Agenda

## - Status update - BOM - Suggested tasks - Micro-Ros - Documentation

# Status

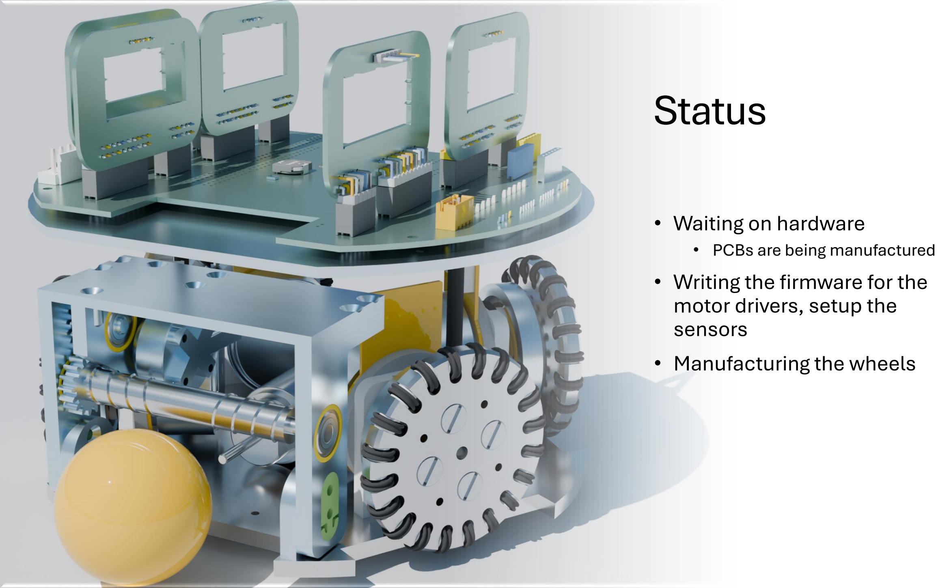
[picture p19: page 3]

- Waiting on hardware
- PCBs are being manufactured
- Writing the firmware for the motor drivers, setup the
sensors
- Manufacturing the wheels

# BOM

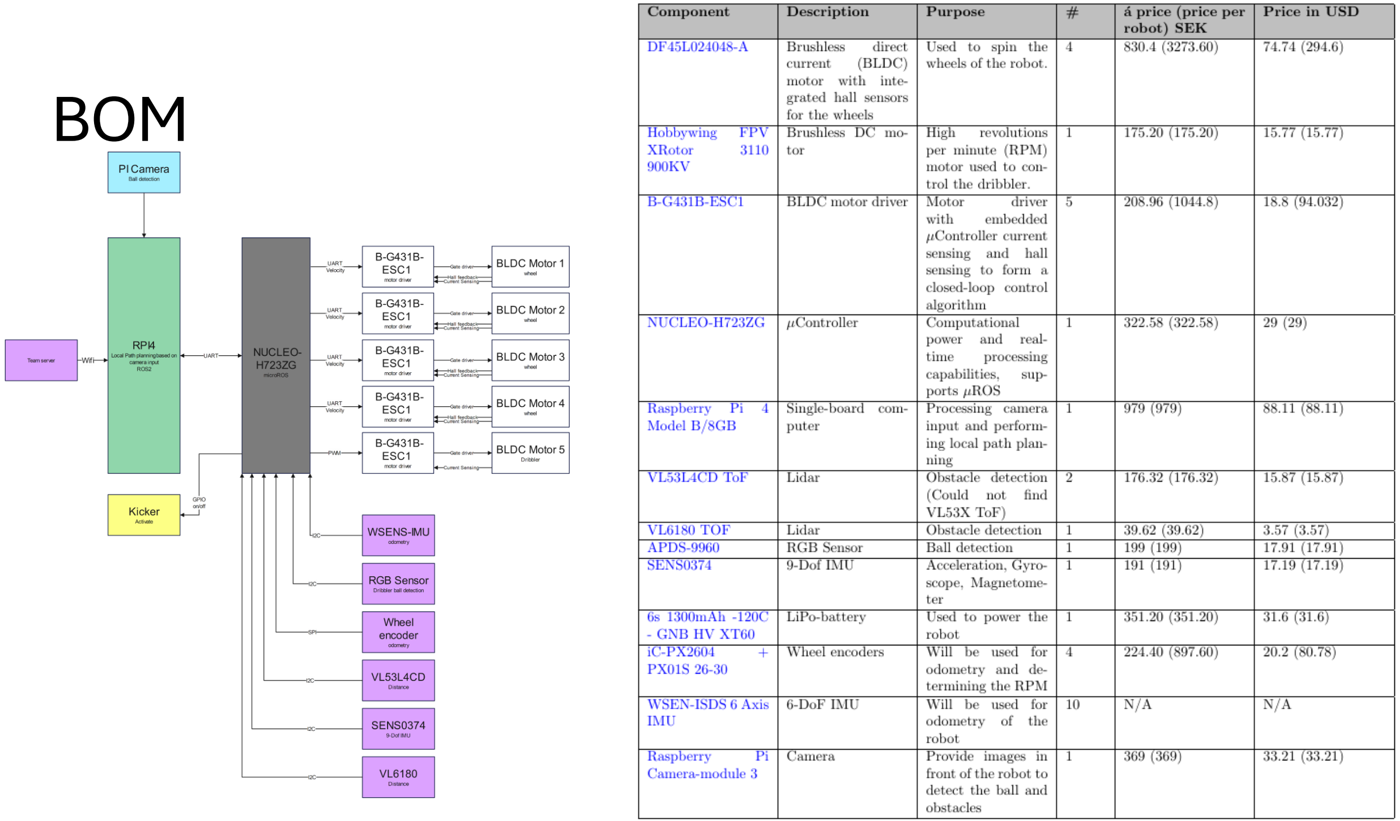
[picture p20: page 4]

# Tasks

## - Hardware interface for the sensor

### oVL53L1

- Get distance

### oVL6180

- Get distance

### oBNO055

- Get acceleration

### oAS5600

- Get angle

### oMotor interface

- Set speed

# Micro-Ros

## - Why ROS2?

- Requirement from the stakeholders to use ROS2 in this project.
- Our software team has been working with ROS2 with the simulation and then to integrate the software with the real hardware, writing the robot firmware using ROS2 would make the integration easier.

# How does ROS2 work

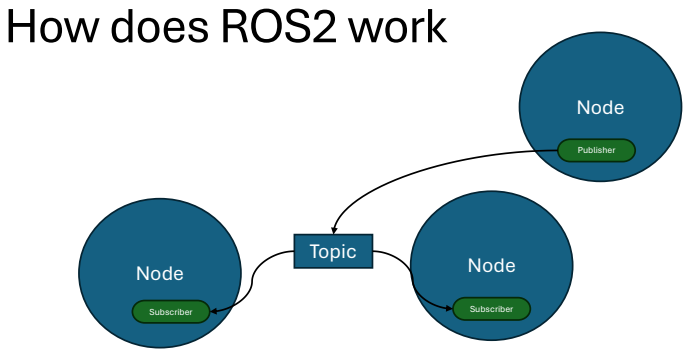
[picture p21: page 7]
Node; Subscriber; Topic; Publisher

# How does ROS2 work

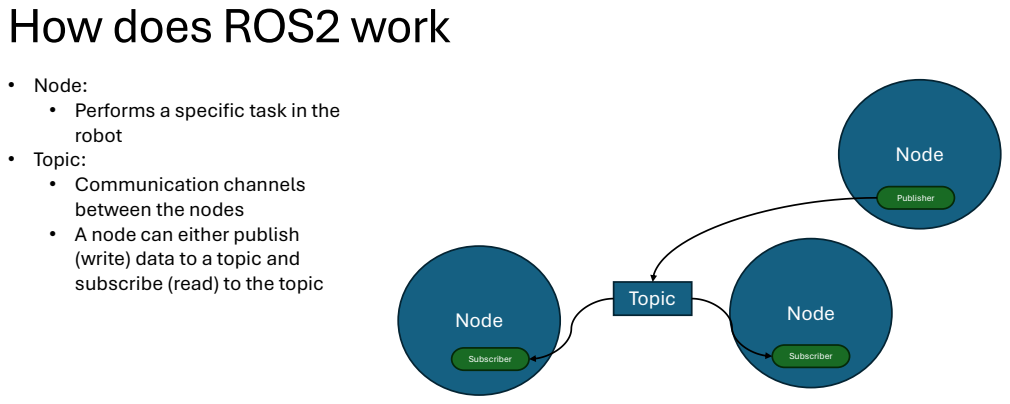
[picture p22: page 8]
Node; Subscriber; Topic; Publisher

• Node:
• Performs a specific task in the
robot
• Topic:
• Communication channels
between the nodes
• A node can either publish
(write) data to a topic and
subscribe (read) to the topic

# How does ROS2 work - Example

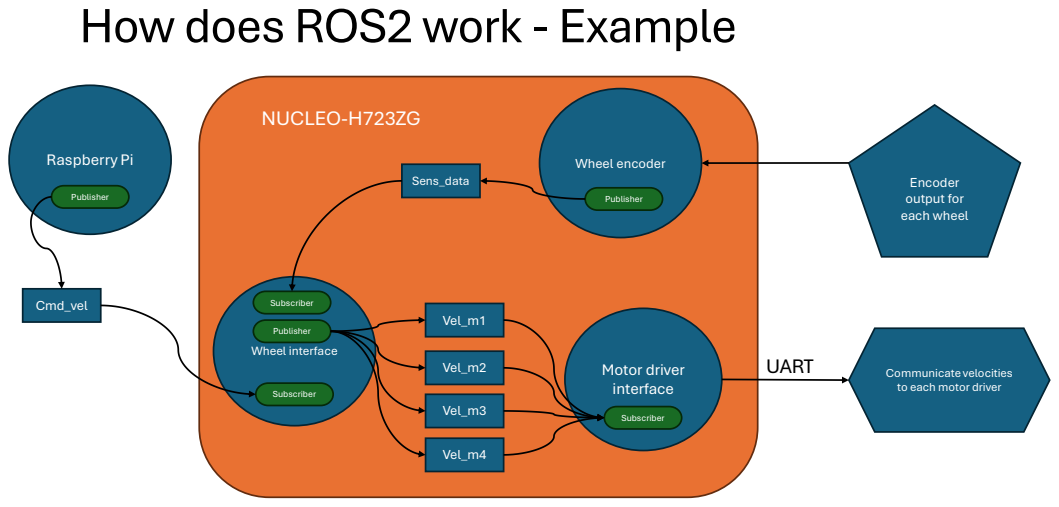
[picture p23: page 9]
Wheel interface; Cmd_vel; Subscriber; Raspberry Pi; Publisher; Vel_m1; Vel_m2; Vel_m3; Vel_m4; Motor driver interface; UART; Wheel encoder; Sens_data; Encoder output for each wheel; NUCLEO-H723ZG

Communicate velocities
to each motor driver

# How does ROS2 work - Resources

### - How to setup micro-ros on nucleo: https://github.com/lFatality/stm32_micro_ros_setup

- Video: https://www.youtube.com/watch?v=xbWaHARjSmk&t=1s

### - ROS2 Humble Documentation: https://docs.ros.org/en/humble/index.html - Micro-ROS Supported hardware: https://micro.ros.org/docs/overview/hardware/

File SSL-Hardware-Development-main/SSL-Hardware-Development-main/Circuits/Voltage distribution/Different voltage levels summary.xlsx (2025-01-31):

Component/Sensor | Voltage level 3.3 | Voltage level 5.0 | Voltage level 12V | Voltage level 15V | Voltage level 24V
LEDEX 195207-228 |  |  | x (continous) |  | x (intermittent)
IR Break Beam 5mm LEDs | x | x (preferred)
Raspberry Pi 3 model A+ |  | x
WSEN-ISDS 6 Axis IMU | x
iC-PX2604 + PX01S 26-30 |  | x (5.0V (±0.5))
ESP32-WROVER-IE | x (DC 3.3V/0.5A)
Moetus R4 |  |  |  |  | x (DC 10V-44V Since we have 24V that is most likely what we will use)
Turnigy Multistar 4225-610Kv 16Pole Multi-Rotor Outrunner |  |  |  | x (MAX 15V)

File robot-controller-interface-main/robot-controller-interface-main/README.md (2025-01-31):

Robot Controller Interface
=======================

About
-----------------------
This repository contains the executable code intended for running on the 
individual robots (on the raspberry pi), termed Individual Robot Behaviour, 
and the accompanying Raspberry Pi part of the Hardware interface API.

### Built with
The Robot Controller Interface is built with the following:

- [ROS2 Humble](https://docs.ros.org/en/humble/index.html)
- [nav2](https://docs.nav2.org/)
- [SLAM Toolbox](https://github.com/SteveMacenski/slam_toolbox)

Getting started
-----------------------

### Prerequisites
On Ubuntu and other Debian derivatives, CMake can be installed with:
```
sudo apt install build-essential cmake
```

For ros2 humble see: https://docs.ros.org/en/humble/Installation/Ubuntu-Install-Debs.html

For nav2 see: https://docs.nav2.org/getting_started/index.html#installation

For SLAM Toolbox see: https://docs.nav2.org/tutorials/docs/navigation2_with_slam.html

### Installation
1. Clone the repository:
```
git clone https://github.com/DVA490-474-Project-Course/robot-controller-interface.git
```
2. Navigate to the project directory:
```
cd robot-controller-interface
```
3. Create a build directory and navigate to it:
```
mkdir build & cd build
```
4. Build the source code:
```
cmake ..
make
```
5. Locate the binaries which should be stored in bin:
```
cd ../bin
```
6. Execute the desired binaries.

Usage
-----------------------

To use individual robot behaviour (path planning etc), then the following 
preconditions must be started:
Start SLAM Toolbox (this requires publishing LIDAR values on the /scan topic):
```
ros2 launch slam_toolbox online_async_launch.py
```
Start the nav2 stack (This requires SLAM Toolbox and odometry being published 
on /odom topic):
```
ros2 launch nav2_bringup navigation_launch.py
```

Examples
-----------------------

### Path planning
An example showing the functionality of the path planning can be seen by doing 
the following (this also requires the Gazebo simulation environment, see 
https://docs.nav2.org/getting_started/index.html):
Start Gazebo:
```
ros2 launch turtlebot3_gazebo turtlebot3_world.launch.py
```
Start SLAM Toolbox:
```
ros2 launch slam_toolbox online_async_launch.py
```
Start the nav2 stack:
```
ros2 launch nav2_bringup navigation_launch.py
```
Run the following binary available in the robot-controller-interface/bin/ 
(bin in this projects root):
```
./main_test_exe --gtest_also_run_disabled_tests --gtest_filter=DwbControllerTest.DISABLED_SendTargetPoseTest
```

### Angle towards target and shoot (ShootSetup)
No examples available.

Roadmap
-----------------------
API:
- [ ] Develop Hardware Interface

Individual Robot Behaviour (executable):
- [x] Develop Path planning 
- [x] Develop robot ability to shoot
- [ ] nav2 stack configuration
- [ ] Integrate Hardware Interface
- [ ] Ability to send data
- [ ] Ability to receive data
- [ ] Initilization of robot

Design diagrams
-----------------------
Design diagrams/files can be found in the [docs](/docs) directory. Additionally 
they are available on:
- [Hardware Interface](https://www.mermaidchart.com/raw/11c442f5-192c-4ac3-b61e-867a3e2ca6ea?theme=dark&version=v0.1&format=svg)
- [Individual Robot Behaviour](https://www.mermaidchart.com/raw/dc459e07-4c98-46b8-8ac0-41c56aa6950f?theme=dark&version=v0.1&format=svg)

License
-----------------------
Distributed under the MIT License. See [License](/LICENSE) for more information.

Contributors and contact
-----------------------
- Aaiza Aziz Khan: akn23018@student.mdu.se
- Carl Larsson: cln20001@student.mdu.se
- Shruthi Puthiya Kunnon: spn23001@student.mdu.se
- Emil Åberg: eag24002@student.mdu.se

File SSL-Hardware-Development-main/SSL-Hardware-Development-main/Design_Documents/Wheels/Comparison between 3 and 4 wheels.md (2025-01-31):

| **Configuration** | **Advantages** | **Disadvantages** |
| --- | --- | --- |
| **4 Wheels** | - Better floor traction, reduced slippage<br>- More acceleration<br>- Increased stability<br>- Proven success (winning teams use 4 wheels)<br>- Full omni-directional movement (3 DoF) | - Higher cost<br>- Increased energy consumption<br>- More complex mechanics and control systems |
| **3 Wheels** | - Mechanically simpler<br>- Easier to control<br>- Lower cost<br>- Full omni-directional movement (3 DoF) | - Lower floor traction<br>- Less stability<br>- Reduced acceleration<br>- Static stability can hinder quick turns and adaptability to dynamic changes |

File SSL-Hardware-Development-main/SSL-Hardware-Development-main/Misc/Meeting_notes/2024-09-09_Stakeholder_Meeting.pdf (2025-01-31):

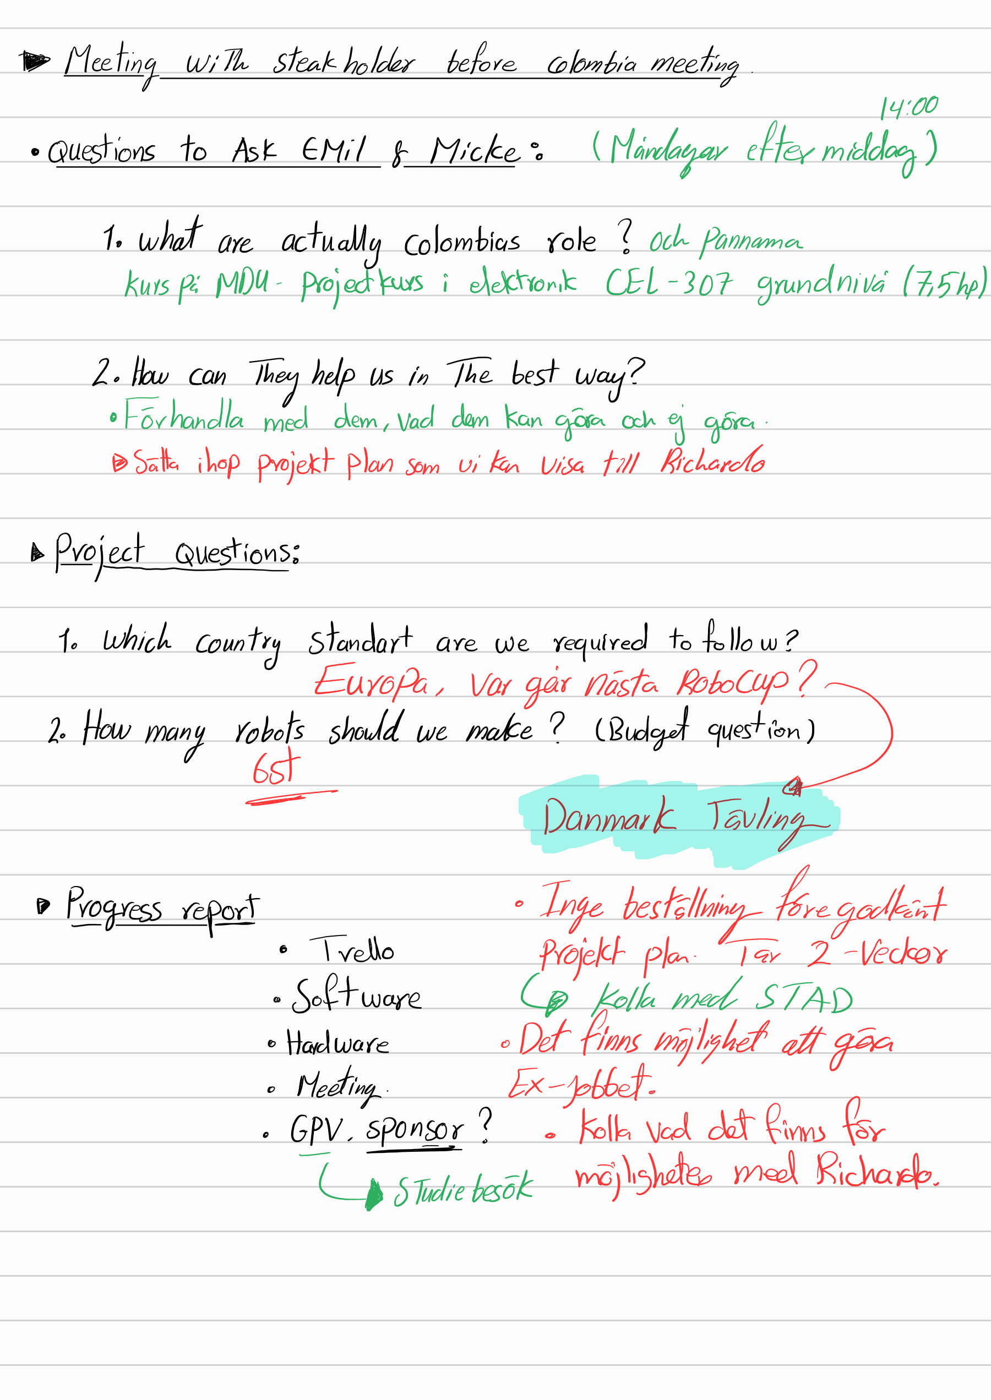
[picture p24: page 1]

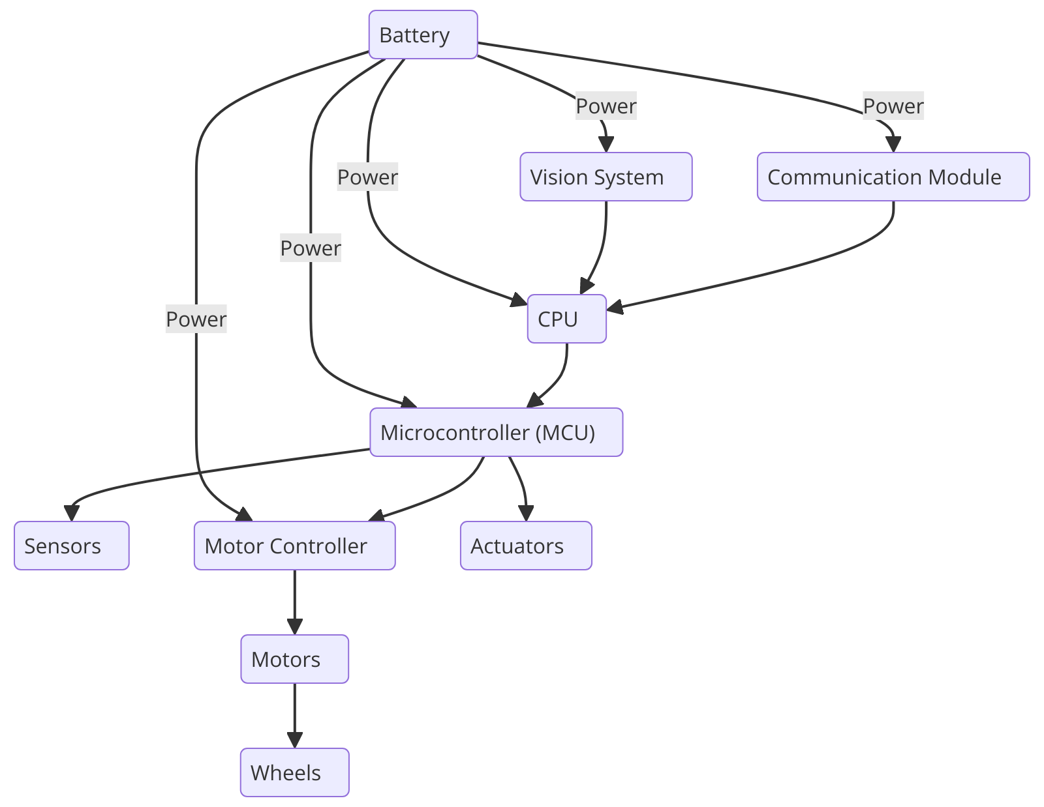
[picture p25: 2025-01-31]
SSL-Hardware-Development-main/SSL-Hardware-Development-main/Misc/diagram.png

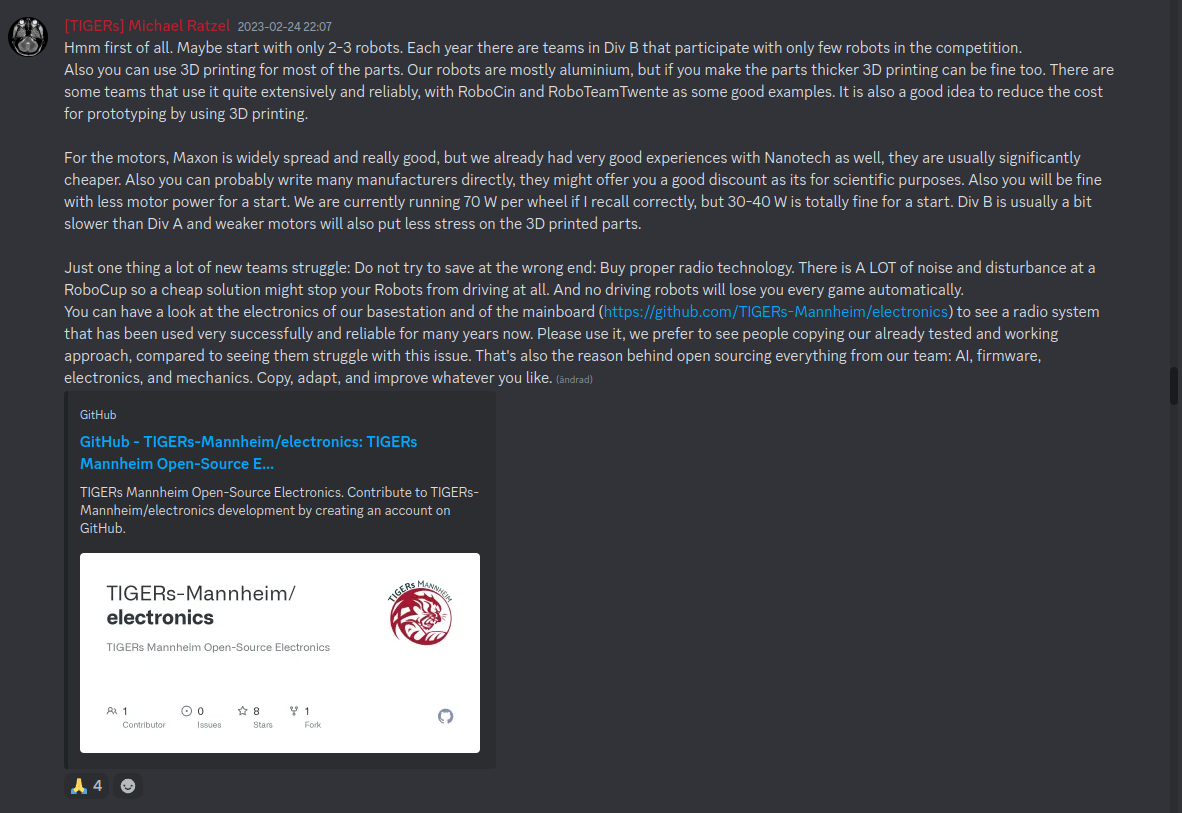
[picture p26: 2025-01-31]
SSL-Hardware-Development-main/SSL-Hardware-Development-main/Misc/knwoledge_from_tigers.png

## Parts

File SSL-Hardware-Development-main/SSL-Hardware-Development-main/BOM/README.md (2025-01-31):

# BOM

The BOM in this folder will continually be updated when new hardware changes are made.

## Updating the BOM
Adhere to the original layout in the BOM document.

- Main file BOM.xlsx

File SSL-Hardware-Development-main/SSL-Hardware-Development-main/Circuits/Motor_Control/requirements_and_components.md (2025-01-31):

### 1. **General Requirements and Component Overview**

#### Key Components:
- **STSPIN32F0 Motor Driver IC**
- **6x N-Channel MOSFETs** (e.g., SQS178ELNW-T1_GE3) for three-phase control
- **Shunt Resistors** for current sensing (if you want to implement current sensing)
- **Hall Sensor Interface** for position feedback from the motor
- **Bootstrap Capacitors** for high-side MOSFET gate driving
- **Decoupling Capacitors** for power stability
- **Programming and Debugging Connectors** (SWD and UART)
- **Power Supply and Filtering Circuitry** for stable operation

#### Suggested PCB Sections:
1. **Power Supply Section**:
   - 24V input with bulk capacitors and protection diodes.
   - Voltage regulators (if needed) for 12V or 5V supply lines.

2. **Gate Driver Section**:
   - Connect STSPIN32F0 gate driver outputs to MOSFET gates.
   - Bootstrap capacitors for high-side MOSFETs.

3. **Motor Output Section**:
   - Three-phase motor outputs (U, V, W).
   - Shunt resistors for each phase for current sensing.

4. **Feedback and Control Section**:
   - Hall sensor inputs for rotor position feedback.
   - Current sensing signals routed to STSPIN32F0 op-amp inputs.

5. **Programming and Debugging Section**:
   - SWD (Serial Wire Debug) connector for programming the STSPIN32F0.
   - UART/USART connector for debugging and communication with ESP32.

6. **Connectors and Test Points**:
   - Motor phase connectors (U, V, W).
   - Hall sensor connector.
   - Probing points for debugging and signal measurement.

### 2. **Detailed Component Selection and Circuit Design**

#### A. **STSPIN32F0 Core Circuit**

1. **Power Supply:**
   - Connect a 24V power supply to the VM pin of the STSPIN32F0.
   - Use a bulk capacitor (e.g., 100µF) at the VM input for filtering.
   - Place decoupling capacitors (100nF and 10µF) close to the VCC and VREG pins for stability.
   - **VREG** provides a regulated voltage (typically 12V) used for driving the gates of the MOSFETs.

2. **Bootstrap Capacitors:**
   - Place 100nF bootstrap capacitors between each VBOOTx and SHx pins (e.g., VBOOTW and OUTW) to provide the high-side gate drive voltage for each phase.

3. **Gate Drive Outputs:**
   - Connect the STSPIN32F0’s high-side (HSU, HSV, HSW) and low-side (LSU, LSV, LSW) gate driver outputs to the MOSFET gates.
   - Place 10Ω gate resistors in series to dampen high-frequency oscillations.

4. **Current Sensing:**
   - Use shunt resistors (e.g., 0.01Ω to 0.05Ω, 1% tolerance) between the source of each low-side MOSFET and ground.
   - Connect the voltage across the shunt resistors to the STSPIN32F0’s internal op-amps (ISEN inputs) to measure the phase current.

5. **Hall Sensor Inputs:**
   - Connect the Hall sensor outputs (H1, H2, H3) from the motor to the Hall sensor input pins (e.g., PA0, PA1, PA2) on the STSPIN32F0.
   - Use pull-up resistors (e.g., 10kΩ) for the Hall sensor lines to ensure clean signals.

#### B. **MOSFET Connections**

1. **High-Side MOSFETs:**
   - Connect the **drain** of each high-side MOSFET to the VM (24V power supply).
   - Connect the **source** of each high-side MOSFET to the respective motor phase (U, V, W).

2. **Low-Side MOSFETs:**
   - Connect the **drain** of each low-side MOSFET to the respective motor phase (U, V, W).
   - Connect the **source** of each low-side MOSFET to ground through the shunt resistors.

3. **Gate Connections:**
   - Connect the gates of the high-side MOSFETs to the HSU, HSV, HSW pins.
   - Connect the gates of the low-side MOSFETs to the LSU, LSV, LSW pins.

#### C. **Programming and Debugging Connectors**

1. **SWD Programming Connector:**
   - Use a 4-pin or 5-pin header for SWD programming.
   - Connect the following pins:
     - **SWDIO**: Data input/output pin for debugging.
     - **SWCLK**: Clock input for debugging.
     - **NRST**: Reset pin (optional but recommended).
     - **GND**: Ground connection.

2. **UART Debugging:**
   - Use a 3-pin or 4-pin header for UART communication (TX, RX, GND, and optional 5V).
   - Configure the STSPIN32F0’s UART pins (e.g., PA9, PA10) for serial communication.
   - This interface can be used for logging, debugging, and communication with the ESP32.

3. **Test Points:**
   - Place test points at key nodes:
     - **PWM Signals**: Check for gate drive signals.
     - **Motor Phases (U, V, W)**: Monitor the motor phase voltage.
     - **Current Sensing**: Measure the voltage across shunt resistors.

#### D. **Connectors for External Components**

1. **Motor Phase Connector:**
   - Use a 3-pin connector for the motor phases (U, V, W).

2. **Hall Sensor Connector:**
   - Use a 5-pin or 6-pin connector for the Hall sensors.
   - Connect the Hall sensor outputs, power, and ground.

3. **Power Connector:**
   - Use a 2-pin power connector for the 24V input.

### 3. **Schematic Layout in KiCad**

1. **Create a New Project:**
   - Create a new schematic and PCB layout project in KiCad.

2. **Place the Components:**
   - Add the STSPIN32F0, MOSFETs, shunt resistors, capacitors, and connectors.
   - Organize components by function (power supply, gate drivers, motor connections).

3. **Draw Connections:**
   - Draw the connections according to the circuit described above.
   - Use labels for common signals like GND, VM, and PWM.

4. **Review and Annotate:**
   - Annotate the schematic to assign component designators (e.g., R1, C1, Q1).

### 4. **PCB Layout Considerations**

1. **Placement:**
   - Place the STSPIN32F0 in a central position, with the MOSFETs arranged around it to minimize gate drive trace lengths.
   - Keep high-current paths (e.g., power input and motor phases) wide and short.

2. **Routing:**
   - Route the gate drive signals with a focus on minimizing resistance and inductance.
   - Use thick traces or copper pours for high-current paths like VM and ground.

3. **Ground Planes and Power Planes:**
   - Use separate ground planes for power and signal grounds if possible.
   - Ensure good decoupling and grounding for the STSPIN32F0 to avoid noise issues.

### 5. **Generating Gerber Files and BOM**

1. **Generate Gerber Files:**
   - Once the layout is complete, generate the Gerber files for PCB fabrication.

2. **Create Bill of Materials (BOM):**
   - Include all components used, with part numbers, quantities, and footprints.

### 6. **Testing and Debugging After Fabrication**

1. **Populate the Board:**
   - Solder the components onto the PCB.

2. **Initial Power-Up:**
   - Check the power supply section first. Ensure that VM and VCC are stable before powering the STSPIN32F0.

3. **Programming the STSPIN32F0:**
   - Use the SWD connector to program the microcontroller using STM32CubeIDE.

4. **Motor Testing:**
   - Connect the motor and test the PWM signals and commutation logic.

This guide should help you create a robust motor control circuit for your project. Let me know if you need any specific help or additional details for any step!

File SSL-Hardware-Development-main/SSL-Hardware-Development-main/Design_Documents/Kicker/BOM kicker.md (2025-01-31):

## Solenoid 

| Name | Price | Size | Coil voltage | Holding Force | Coil Resistance | Weigth | P | |
| --- | --- | --- | --- | --- | --- | --- | ----- | --- |
| LEDEX 195207-228 | 262.83 Kr (farnell) | 25.4 mm x 50.80 mm | 13.8VDC | 28.9N | 19.2 ohm | 190.8g | | |
| AS-PL SS0017 | 236.97 kr (autodoc) | | | | | Ca 300 g | | |
| Solenoid 41013986 | 359 kr (electrokit) | 89x38x30mm | 36VDC | | | 331g | 99.7W | |
| Delta electronics DSMS-0730-12 | 230.45 | | 12VDC | | 4.5 ohm | 40.2g | 3.8W  | |
| DSOS-0416-09D | 92.89 | | 9VDC | | 22.6ohm | | | |

### LEDEX 195207-228  
- The solenoid needs to be light weighted and not to expensive. It needs to be able to kick the golf ball.
- Henrik has ordered LEDEX 195207-228            

## IC  (Capacitor charger Controller)

| Name | Price | Max V |  Website  |
| --- | --- | ----- | --- |
| LT3750 | 149 kr (digikey), 75 kr (farnell) | 3-24V |  https://www.digikey.se/en/products/detail/analog-devices-inc/LT3750AEMS-PBF/14683705 |

### Reasons for LT3750: 
- Charges Any Size Capacitor
- Easily Adjustable Output Voltage
- Drives High Current NMOS FETs
- Primary-Side Sense—No Output Voltage Divider Necessary
- Wide Input Range: 3V to 24V
- Drives Gate to VCC – 2V
- Available in 10-Lead MS Package
- Emergency Warning Beacons
- Professional Photoflash Systems
- Security/Inventory Control Systems
- High Voltage Power Supply
- Electric Fences
- Detonators

| Name | Price | Max V | Website |
| --- | --- | ----- |--- |
| Capacitor  |  | | |
| Diod  |  | | |
| DA2034-ALD  | 98,56  | |  https://www.mouser.se/ProductDetail/Coilcraft/DA2034-ALD?qs=ZYnrCdKdyedtN304hL7iMg%3D%3D |

### Reasons for Capacitor
The capacitor is needed to provide hight voltage to the solenoid so that it can kick the golfball.  
### Reasons for Diod
To prevent backfeed
### Reasons for Transformer
This component is needed for LT3750

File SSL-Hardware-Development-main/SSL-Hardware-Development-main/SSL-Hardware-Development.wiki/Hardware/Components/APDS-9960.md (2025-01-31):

# Motor for the Wheels
## Info

- **Name**: [Turnigy Multistar 4225-610Kv](https://hobbyking.com/en_us/turnigy-multistar-4225-610kv-16pole-multi-rotor-outrunner.html?___store=en_us#qa[bW9kZT03JnBhZ2U9MSZxdWVzdGlvbl9zZWFyY2hfY29udGVudD0=])
- **Datasheet**: N/A

| **Specification** | **Value** |
|---|---|
| **KV (RPM/V)** | 610 KV |
| **Weight** | 130g |
| **Dimensions** | 42mm x 25mm |
| **Max Current** | 25A |
| **Max Power (10S)** | 640W |
| **Idle Current (10V)** | 0.8A |
| **Resistance** | 0.120 ohms |
| **Max Voltage** | 4S (16.8V) |
| **Shaft Diameter** | 4mm |
| **No. of Cells (LiPo)** | 4S |
| **Max Thrust (with recommended prop)** | 1360g (using 13x4.5 propeller) |
| **Number of Poles** | 16 poles |
| **Mounting Holes Spacing** | 19mm / 25mm (M3 thread) |
| **Max Efficiency** | 87% |

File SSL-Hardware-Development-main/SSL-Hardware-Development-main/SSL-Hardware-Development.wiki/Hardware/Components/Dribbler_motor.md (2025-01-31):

# Dribbler Motor
## Info

- **Name**: **[Hobbywing FPV XRotor 3110 900KV](https://www.elefun.se/p/prod.aspx?v=65193)**
- **Description**: FPV motor from XRotor series designed for 4-6S LiPo batteries.

| **Specification** | **Value** |
|---|---|
| **Motor Type** | Brushless DC (BLDC) |
| **Nominal Voltage** | 4-6S LiPo |
| **KV Rating** | 900 KV |
| **Max Power** | 1500 W (for 10 seconds) |
| **Max Thrust** | 3626 g |
| **Dimensions** | 37.2 x 27 mm |
| **Weight** | 89 g |
| **Shaft Length** | 16 mm |
| **Wire Length** | 250 mm |
| **Cable Type** | 18 AWG |

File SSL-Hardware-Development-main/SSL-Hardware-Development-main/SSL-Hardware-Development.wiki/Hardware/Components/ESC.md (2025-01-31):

# Electronic Speed Controller

## Description
The Electronic Speed Controller (ESC) is necessary to control the BLDC motors used for the wheels

## Requirements
1. **Bidirectional Control**
   - The motors need to run both forwards and backwards. ESC must be bidirectional

2. **Customization**
   - Ability to configure acceleration curves and braking is necessary

3. **Communication Interface**
   - The ESCs should accept control inputs from an [NUCLEO-H723ZG](https://github.com/DVA490-474-Project-Course/SSL-Hardware-Development/wiki/Microcontroller) (e.g. PWM, UART, CAN)
   - The ESC should provide feedback which can be used to improve the control precision. (e.g. EMF)

4. **Motor Compatibility**:  
   - Compatible with brushless motors ([DF45L024048-A](https://github.com/DVA490-474-Project-Course/SSL-Hardware-Development/wiki/Motor_Wheel)).
   - Voltage and current ratings meet or exceed motor specifications.

5. **Physical Size and Weight**:  
   - Fits within the physical constraints of your robot's design.
   - Consideration of overall weight to maintain performance.

6. **Power Management**:  
   - Integrated Battery Eliminator Circuit (BEC), needed to power electronics.
   - Efficient power usage to maximize battery life.

## **[B-G431B-ESC1](https://www.st.com/en/evaluation-tools/b-g431b-esc1.html)**

| **Specification** | **Value** |
|---|---|
| **Microcontroller** | STM32G431CB (32-bit ARM Cortex-M4)|
| **Voltage Range** | 8 V to 28 V |
| **Continuous Current** | Up to 15 A |
| **Peak Current** | 40 A |
| **Motor Type** | Brushless DC (BLDC) |
| **Control Algorithm** | Field-Oriented Control (FOC) & 6 step commutation |
| **PWM Frequency** | Configurable, up to 100 kHz |
| **Communication Interfaces** | UART, CAN, PWM|
| **Sensor Compatibility** | Hall sensors, Encoder, Sensorless |
| **Dimensions** | 30 mm x 41 mm |
| **Weight** | Approx. 9.2 g |
| **Programming Options** | ST-Link Debugger, STM32CubeIDE |
| **Protection Features** | Overcurrent, Overvoltage, Overtemperature |

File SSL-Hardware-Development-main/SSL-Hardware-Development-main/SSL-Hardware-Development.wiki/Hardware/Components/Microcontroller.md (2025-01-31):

# Microcontroller
## Info

- **Name**: [NUCLEO-H723ZG](https://www.st.com/en/evaluation-tools/nucleo-h723zg.html)

| **Specification** | **Details** |
|---|---|
| **Microcontroller** | STM32H723ZG (ARM® Cortex®-M7 core, 550 MHz) |
| **Flash Memory** | 1 MB |
| **SRAM** | 564 KB (128 KB Data TCM RAM, 432 KB System RAM, and 4 KB Backup SRAM) |
| **Clock Speed** | Up to 550 MHz |
| **Operating Voltage** | 1.62 V to 3.6 V |
| **Power Supply Options** | - USB VBUS<br>- External sources via VIN (7 V to 12 V) or 5V_EXT (5 V) |
| **Connectivity** | - Ethernet compliant with IEEE-802.3-2002<br>- USB 2.0 high-speed/full-speed device/host/OTG controller<br>- 5× I2C<br>- 5× USART/UART<br>- 6× SPI<br>- 2× CAN |
| **Expansion Interfaces** | - ST Zio connector (Arduino Uno V3 compatibility)<br>- ST morpho headers |
| **Debug Interface** | On-board ST-LINK debugger/programmer with USB re-enumeration capability (mass storage, Virtual COM port, and debug port) |
| **User Interface** | - 3 user LEDs<br>- 2 user push-buttons<br>- Reset push-button |
| **Dimensions** | 147 mm x 90 mm |
| **Weight** | Approximately 100 g |
| **Supported IDEs** | - STM32CubeIDE<br>- IAR Embedded Workbench®<br>- MDK-ARM |
| **Additional Features** | - 32.768 kHz crystal oscillator<br>- Free software libraries and examples available with STM32Cube MCU Package |

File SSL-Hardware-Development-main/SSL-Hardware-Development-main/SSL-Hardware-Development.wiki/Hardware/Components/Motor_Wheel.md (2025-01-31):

# Motor for the Wheels

The DF45L024048-A is a brushless direct current motor (BLDC). It has integrated hall sensors spaced 120 degrees apart which is used to activate the gate drivers.
## Info

- **Name**: **[DF45L024048-A](https://www.nanotec.com/eu/en/products/1786-df45l024048-a)**
- **Datasheet**: **[DF45L024048-A Datasheet](https://www.nanotec.com/fileadmin/files/Datenblaetter/BLDC/DF45/DF45L024048-A.pdf?1656012533)** 

| **Specification** | **Value** |
|---|---|
| **Motor Type** | Brushless DC (BLDC), Outer Rotor  |
| **Nominal Voltage** | 24 V |
| **Rated Current** | 6.4 A |
| **Nominal Power** | 151 W |
| **Rated Speed** | 3175 rpm |
| **Torque Constant (Kt)** | 0.045 Nm/A |
| **Resistance** | 1.2 Ω |
| **Inductance** | 0.4 mH |
| **Rotor Inertia** | 13 g·cm² |
| **Weight** | 320 g |
| **Shaft Diameter** | 5 mm |
| **Outer Diameter** | 45 mm |
| **Length** | 48 mm |
| **Encoder Option** | Hall sensors |

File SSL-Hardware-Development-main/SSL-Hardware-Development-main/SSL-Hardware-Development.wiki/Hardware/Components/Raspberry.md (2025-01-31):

# Raspberry Pi
## Info

- **Name**: [Raspberry Pi 4 Model B](https://www.raspberrypi.org/products/raspberry-pi-4-model-b/)
- **Datasheet**: [Raspberry Pi 4 Datasheet](https://datasheets.raspberrypi.com/rpi4/raspberry-pi-4-datasheet.pdf)

| **Specification** | **Value** |
|---|---|
| **Processor** | Broadcom BCM2711, Quad-core Cortex-A72 (ARM v8) 64-bit SoC @ 1.5GHz |
| **Memory** | 2GB, 4GB, or 8GB LPDDR4-3200 SDRAM |
| **Networking** | Gigabit Ethernet, 2.4 GHz and 5.0 GHz IEEE 802.11b/g/n/ac wireless LAN, Bluetooth 5.0 |
| **USB Ports** | 2 × USB 3.0, 2 × USB 2.0 |
| **Video Outputs** | 2 × micro HDMI ports (supports up to 4Kp60) |
| **Power Input** | 5V DC via USB-C connector or GPIO header (minimum 3A for full load) |
| **GPIO** | 40-pin GPIO header (backward compatible with previous Raspberry Pi boards) |
| **Storage** | microSD card slot |
| **Dimensions** | 85.6mm × 56.5mm |
| **Weight** | 46g |
| **Operating System** | Raspberry Pi OS, compatible with Linux distributions |
| **Power-over-Ethernet (PoE)** | Enabled with PoE HAT (optional) |
| **Dual-display Support** | Up to 4Kp60 on dual monitors |
| **Video Decode** | Hardware decoding of H.265 (4Kp60), H.264 (1080p60) |

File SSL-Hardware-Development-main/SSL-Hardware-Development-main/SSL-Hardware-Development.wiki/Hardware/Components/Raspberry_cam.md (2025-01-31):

# Motor for the Wheels
## Info

- **Name**: [Turnigy Multistar 4225-610Kv](https://hobbyking.com/en_us/turnigy-multistar-4225-610kv-16pole-multi-rotor-outrunner.html?___store=en_us#qa[bW9kZT03JnBhZ2U9MSZxdWVzdGlvbl9zZWFyY2hfY29udGVudD0=])
- **Datasheet**: N/A

| **Specification** | **Value** |
|---|---|
| **KV (RPM/V)** | 610 KV |
| **Weight** | 130g |
| **Dimensions** | 42mm x 25mm |
| **Max Current** | 25A |
| **Max Power (10S)** | 640W |
| **Idle Current (10V)** | 0.8A |
| **Resistance** | 0.120 ohms |
| **Max Voltage** | 4S (16.8V) |
| **Shaft Diameter** | 4mm |
| **No. of Cells (LiPo)** | 4S |
| **Max Thrust (with recommended prop)** | 1360g (using 13x4.5 propeller) |
| **Number of Poles** | 16 poles |
| **Mounting Holes Spacing** | 19mm / 25mm (M3 thread) |
| **Max Efficiency** | 87% |
## Reason
This component provides a good tradeoff between torque, RPM and price.
Ideally we would want a high torque at low speeds for fast acceleration and high RPM. This motor provides a sufficient torque at low speeds but can still reach high RPM values.

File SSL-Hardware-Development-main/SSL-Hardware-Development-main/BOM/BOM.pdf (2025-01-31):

BOM

Part name | Quantity
DF45L024048-A – Brushless DC motor | 4
Hobbywing FPV XRotor 3110 900KV | 1
6s 1300mAh -120C - GNB HV XT60 | 1
M3 16mm galvanized steel countersunk screw, 100 pack | 1
M3 galvanized steel locking washers, 200 pack | 1
M3 steel locking washers, 200 pack | 1
M3 stainless steel nut, 100 pack | 1
PHR-6 | 8
B6B-PH-K-S | 10
VHR-5N | 10
Bearings with flange iglidur® M250 | 200
X-RING 3.63X2.62/NBR70 | 100
SEN0374 | 1
Raspberry Pi RTC | 1
| 2
LM74500QDDFRQ1 | 2
BUK9Y8R5-80EX | 2
NUCLEO-H723ZG | 1
SX1280IMLTRT | 1
SKY66122-11 | 1
B-G431B-ESC1 | 5
Wheel hub 4mm | 4
Raspberry Pi 4 Model B/8GB | 1
Raspberry Pi Kameramodul 3 | 1
Bearings 5mm | 6
M3 threaded inserts 3mm, 50 pack | 1
APDS-9960 | 1
TOF400C-VL53L1 | 1
VL6180 TOF | 1
XT60PW-M | 1
2-post pillow block, 32mm bore | 4
B5P-VH | 10
OFFERT finns för nedanstående, se bifogad fil
OFFERT – BROADCOM AEDB-9140-A13 | 8

LT3751

Distributor

https://www.nanotec.com/eu/en/products/1786-df45l024048-a
https://www.elefun.se/p/prod.aspx?v=65193
https://www.elefun.se/p/prod.aspx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
https://www.elfa.se/sv/lasbricka-m3-stal-bossard-az-2x6x0-cll4880/p/30071831https://www.elfa.se/sv/sexkantsmutter-m3-4mm-rostfritt-stal-rnd-rnd-610-00485/p/30172720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

https://www.mouser.se/ProductDetail/Analog-Devices/LT3751IFEPBF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

https://www.mouser.se/ProductDetail/511-NUCLEO-H723ZGhttps://www.mouser.se/ProductDetail/Semtech/SX1280IMLTRT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
https://www.electrokit.com/axelnav-med-klamfaste-4mm
https://www.electrokit.com/raspberry-pi-4-model-b/8gb
https://www.electrokit.com/raspberry-pi-kameramodul-3-12mp-75https://www.electrokit.com/kullager-5mmhttps://www.electrokit.com/ganginsats-m3-x-3mm-50-packhttps://www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

https://uk.farnell.com/broadcom-limited/aedb-9140-a13/encoder-3channel-500cpr-8mm/dp/1161087

Distributor Part Number

DF45L024048-A
65193
63197
301-72-632
300-71-826
300-71-831
301-72-720
143-01-984
143-01-948
300-21-738
MFM-0103-02
2111395N70
426-SEN0374
713-103030277

584-LT3751IFE#PBF
595-LM74500QDDFRQ1
771-BUK9Y8R5-80EX

511-NUCLEO-H723ZG
947-SX1280IMLTRT
873-SKY66122-11
511-B-G431B-ESC1
41020172
41017664 - Raspberry Pi
41020240 - Raspberry Pi
41019266
41018554
41013512 – Sparkfun

XT60PW-M
RP-Sct-2151
JST (JAPAN SOLDERLESS TERMINALS) B5P-VH(LF)(SN)

BROADCOM AEDB-9140-A13

Manufacturer | Mfr Part number | Á price
| | 818.4
https://www.hobbywing.com/ | HW30418005 | 219
http://www.gaonengbattery.com/ | GNB13006S120AHV | 442
https://www.elfa.se/sv/manufacturer/rnd/man_rnd | RND 610-00397 | 21.6
https://www.bossard.com/se-sv/ | AZ 3,2X6X0,4 | 69.7
https://www.bossard.com/se-sv/ | AZ S 3,2X6X0,4 / CLL4880 S | 83.3
https://www.elfa.se/sv/manufacturer/rnd/man_rnd | RND 610-00485 | 21.85
https://www.elfa.se/sv/manufacturer/jst/man_jst | PHR-6 | 1.07
https://www.elfa.se/sv/manufacturer/jst/man_jst | B6B-PH-K-S | 5.43
https://www.elfa.se/sv/manufacturer/jst/man_jst | VHR-5N | 2.22
https://www.igusab.se/ | MFM-0103-02 | 3.34
| | 6.2
https://www.mouser.se/manufacturer/dfrobot/ | SEN0374 | 191.48
https://www.mouser.se/manufacturer/seeed-studio/ | 103030277 | 1
https://www.mouser.se/manufacturer/analog-devices/ | LT3751IFE#PBF | 147.09
https://www.mouser.se/manufacturer/texas-instruments/ | LM74500QDDFRQ1 | 16.45
https://www.mouser.se/manufacturer/nexperia/ | BUK9Y8R5-80EX | 17.94
https://www.mouser.se/manufacturer/stmicroelectronics/ | NUCLEO-H723ZG | 322.58
https://www.mouser.se/manufacturer/semtech/ | SX1280IMLTRT | 75.44
https://www.mouser.se/manufacturer/skyworks-solutions/ | SKY66122-11 | 40.48
https://www.mouser.se/manufacturer/stmicroelectronics/ | B-G431B-ESC1 | 208.96
https://www.gobilda.com/ | 1309-0016-0004 | 139
https://www.raspberrypi.com/ | | 979
https://www.raspberrypi.com/ | | 369
| | 15
| | 95
https://www.sparkfun.com/ | APDS-9960 | 199
https://www.mouser.se/manufacturer/stmicroelectronics/ | VL53L1CBV0FY/1 | 176.32
https://www.st.com/en/imaging-and-photonics-solutions/vl6180.html VL6180 | 33
https://www.tme.eu/se/katalog/p,amass_1260/ | XT60PW-M | 11.21
https://www.servocity.com/ | 1602-0032 | 172.29
https://se.farnell.com/b/jst-japan-solderless-terminals | B5P-VH(LF)(SN) | 5.21
https://uk.farnell.com/b/broadcom | AEDB-9140-A13 | 309

1 Robot Cost Lead time | Notes

3273.6 In stock
219 In stock | BLDC motor for the dribbler
442 In stock | Battery
21.6 In stock
69.7 In stock
83.3 In stock
21.85 In stock
8.56 In stock | Hall sensor connector for the motor
54.3 In stock | Hall sensor connector for the motor
22.2 In stock | Motor connectors
334 in stock | Price dependent on the amount you buy
620 in stock | Price dependent on the amount you buy
191.48 4 left in stock | 9Dof IMU
47.61 In stock

294.18 In stock
32.9 In stock | Reverse polarity protection
35.88 In stock | Mosfet used with the reverse polarity protection component

322.58 In stock
75.44 In stock | RF Transceiver Long range 2.4 GHz Wireless Transceiver
40.48 In stock | RF Front End OFDM, 863 to 928 MHz, Wi-SUN, FEM
1044.8 In stock | Datasheet
556 in stock
979 In stock | Can be substituted with Raspberry Pi 4 Model B/4GB
369 In stock | Needs to be ordered with Raspberry Pi 4 Model B/8GB or Raspberry Pi 4 Model B/4GB
90 In stock | for dribbler assembly.
95 In stock
199 In stock | Chosen by UdeA, RGB sensor
176.32 In stock | Chosen by UdeA, could not find from another seller
33 In stock | Chosen by UdeA, could not find from another seller
11.21 In stock | XT60 PCB connector
689.16 On demand, 1 month delivery time For extra support for the wheels, compatible with chosen hub.
52.1 In stock | Motor connectors
2472 In stock | Offert från farnell med studentrabatt
12977.25

BLDC motors for the wheels, compact size, light weight, contains hall sensors for encoder feedback Sensored ESC is required if these are used

Capacitor charging controller for kicker

If we do not develop our own pcb this microcontroller can be used instead of the ESP32 microcontroll-Er, ADC, communication, supports micro ros

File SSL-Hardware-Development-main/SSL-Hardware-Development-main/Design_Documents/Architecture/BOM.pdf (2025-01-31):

# Bill of Materials (BOM) Explanation

Pontus Svensson / RoboCup

November 6, 2024

## Contents

1 Introduction | 3
2 BOM | 3
3 Reason for component choice | 4
4 Hardware Architecture | 6

## 1 Introduction

This document provides an explanation of the Bill of Materials (BOM) used in the project. Each component listed in the BOM is described in detail, including its purpose and other relevant specifications.

## 2 BOM

Table 1 below outlines the components used in this project along with their purpose and additional information.

Table 1: Main components

Component | Description | Purpose | # | ´a price (price per robot) SEK | Price in USD
DF45L024048-A (https://www.nanotec.com/fileadmin/files/Datenblaetter/BLDC/DF45/DF45L024048-A.pdf?1656012533) | Brushless direct current (BLDC) motor with inte-grated hall sensors for the wheels | Used to spin the wheels of the robot. | 4 | 830.4 (3273.60) | 74.74 (294.6)
Hobbywing FPV XRotor 3110 900KV (https://www.hobbywing.com/en/products/xrotor3110) | Brushless DC mo-tor | High revolutions per minute (RPM) motor used to con-trol the dribbler. | 1 | 175.20 (175.20) | 15.77 (15.77)
B-G431B-ESC1 (https://www.mouser.se/datasheet/2/389/b-g431b-esc1-1848063.pdf) | BLDC motor driver | Motor driver with embedded µController current sensing and hall sensing to form a closed-loop control algorithm | 5 | 208.96 (1044.8) | 18.8 (94.032)
NUCLEO-H723ZG (https://www.st.com/en/evaluation-tools/nucleo-h723zg.html) | µController | Computational power and real-time processing capabilities, sup-ports µROS | 1 | 322.58 (322.58) | 29 (29)
Raspberry Pi 4 Model B/8GB (https://datasheets.raspberrypi.com/rpi4/raspberry-pi-4-datasheet.pdf) | Single-board com-puter | Processing camera input and perform-ing local path plan-ning | 1 | 979 (979) | 88.11 (88.11)
VL53L4CD ToF (https://learn.adafruit.com/adafruit-vl53l4cd-time-of-flight-distance-sensor?view=all) | Lidar | Obstacle detection (Could not find VL53X ToF) | 2 | 176.32 (176.32) | 15.87 (15.87)
VL6180 TOF (https://www.electrokit.com/upload/product/41013/41013634/DM00112632.pdf) | Lidar | Obstacle detection | 1 | 39.62 (39.62) | 3.57 (3.57)
APDS-9960 (https://docs.broadcom.com/doc/AV02-4191EN) | RGB Sensor | Ball detection | 1 | 199 (199) | 17.91 (17.91)
SENS0374 (https://wiki.dfrobot.com/BNO055_Intelligent_9_Axis_Sensor_Module_SKU_SEN0374) | 9-Dof IMU | Acceleration, Gyro-scope, Magnetome-ter | 1 | 191 (191) | 17.19 (17.19)
6s 1300mAh -120C - GNB HV XT60 (https://www.elefun.se/p/prod.aspx?v=65193) | LiPo-battery | Used to power the robot | 1 | 351.20 (351.20) | 31.6 (31.6)
iC-PX2604 + PX01S 26-30 (https://www.ichaus.de/product/ic-px-series/#documents) | Wheel encoders | Will be used for odometry and de-termining the RPM | 4 | 224.40 (897.60) | 20.2 (80.78)
WSEN-ISDS 6 Axis IMU (https://www.we-online.com/components/products/datasheet/2536030320001.pdf) | 6-DoF IMU | Will be used for odometry of the robot | 10 | N/A | N/A
Raspberry Pi Camera-module 3 (https://www.electrokit.com/upload/product/41020/41020240/Camera_Module_3_Product_Brief.pdf) | Camera | Provide images in front of the robot to detect the ball and obstacles | 1 | 369 (369) | 33.21 (33.21)

## 3 Reason for component choice

### 3.1 DF45L024048-A

During competition a SSL-robot is most of the time accelerating [1]. Having a motor which can provide sufficient torque at any given speed is crucial.
The DF45L024048-A BLDC motors provides a good tradeoff between torque and RPM, with integrated hall sensors. The sensors detect the position of the rotor relative to the stator which gives the ability to control the motors using commutation. The motor controller uses the signals from the hall sensors to determine the exact timing for switching the current in the stator windings. This gives a smooth motor operation while maximizing torque output.
The size of the motor has to be taken into account. Having to large footprint on the motors would cause the kicker (solenoid) to not fit in the chassi. Using a general 5010 sensorless drone motor could be used as demonstrated by [2] but this motor would require a more sophisticated ESC which would take a lot of time to develop and manufacture. The problem with searching for 5010 drone motors is that most websites does not show the full torque graph, they primarly show the torque when the motor is already spinning at 40% throttle and above. Therefore finding a 5010 drone motor with adequate torque at low speeds is deceptively difficult.
Using hall sensors is a common method utilized by several teams and proven to be a winning concept [3][4][5][1].

### 3.2 Hobbywing FPV XRotor 3110 900KV

The requirements for the dribbler motor is that it can reach high RPM (around 10000 RPM). No feedback is implemented for the dribbler motor, due to the timeframe of the project a control algorithm will not be implemented.

### 3.3 B-G431B-ESC1

A sensorless controller requires that the BLDC motor produce a measurable back electromotive force (EMF) so the controller can determine the position of the rotor and therefore cannot provide smooth commutation at start up and low speeds. [6]
The chosen electronics speed controller (ESC) has an STSPIN32F0A system in package chip which has an integrated STM32 processor with hall sensor decoding logic and current sensing capabilities. This makes this ESC a good fit with the DF45L024048-A BLDC motor.
The STSPIN32F0A chip is a common choice for controlling BLDC motors in the SSL competitions which has been proven to be reliable and succesful [3][7].
Field-Oriented control (FOC) can be implemented on the B-G431B-ESC1. Guidance and firmware for the B-G431B-ESC1 has been received from Delft Mercurians that will make the process of implementing this streamlined.
A PID system can be implemented on the chip to allow for precise movement and rapid acceleration which is critical to make fast directions changes.
The B-G431B-ESC1 will receive a desired velocity, to use this within a PID system the RPM of each motor is required. The size and weight of the ESC does also have to be taken in consideration, the B-G431B-ESC1 has a small footprint with a relatively low weight 286g. With all the components integrated on one board will make the assembly process easier and reduce any external components e.g. hall sensing or mosfets. The programming for the integrated STM32 is done using STM32 Motor Control Software Development Kit which is a graphical programming environtment from ST.

### 3.4 NUCLEO-H723ZG Microcontroller

The NUCLEO-H723ZG is a development board based on the STM32H723ZG chip, it comes with all necessary peripheral communication UART, SPI, I2C and CAN. The STM32H723ZG features an ARM Cortex-M7 core operating at up to 480 MHz, providing good processing power for handling multiple real-time tasks required in our application. Additionally, the STM32 series is widely adopted in RoboCup competitions, including the Small Size League (SSL) [3][8][5]. This widespread use underscores its reliability and effectiveness in competititions. By using STM32H723ZG chip, previous teams implementations that is open sourced can be used for guidance when developing.
To manage the various tasks and ensure smooth operation of our robot, the control architecture will be implemeted using micro-ROS in combination with FreeRTOS on the NUCLEO-H723ZG.
FreeRTOS is a real-time operating system that provides task scheduling and resource management. Implementing FreeRTOS on the NUCLEO-H723ZG allows us to handle multiple concurrent tasks efficiently, such as sensor data processing, motor control, and communication with other system components.
By using the STM32H723ZG chip future improvements can be made, without having to replace the hardware and potentially the need to re-program/port using another framework.

### 3.5 Raspberry Pi 4 Model B/8GB

It is important to accurately detect the ball and other robots in a timely manner, therefore a Raspberry Pi camera will be used, and the input image will be processed on the Raspberry Pi 4. The Raspberry pi has been used in the SSL competitions for this purpose [9][10]. A lot of information and open sourced firmware exist.

The Raspberry Pi 4 was also chosen to be able to run the DWA path planning algorithm, due to the timeframe of this project, implementing DWA by ourself would require too much time.

### 3.6 VL53L4CD ToF Sensor

The VL53L4CD ToF (Time-of-Flight) sensor is a laser-based ranging sensor capable of measuring distances with high accuracy. It is used for obstacle detection in the robot, allowing the system to identify obstacles within close proximity. With a range of up to 1300 mm, it is especially suited for detecting obstacles that could interfere with the robot’s navigation. The sensor communicates using I2C, which simplifies integration with the existing hardware.

### 3.7 VL6180 TOF Sensor

The VL6180 TOF sensor, also a Time-of-Flight sensor, serves a similar purpose as the VL53L4CD but operates at shorter distances, making it ideal for near-field obstacle detection. It is also chosen for its compact size and I2C communication, which allows it to seamlessly interface with the microcontroller. The shorter range provides additional resolution for objects very close to the robot, further enhancing obstacle detection accuracy.

### 3.8 APDS-9960 Sensor

The APDS-9960 sensor is a versatile RGB sensor with integrated IR sensing capabilities. It is primarily used in this project for ball detection, as it can distinguish colors and detect the presence of nearby objects. This feature enables the robot to differentiate the ball from the surroundings based on color and proximity. Communication is handled via I2C, allowing for easy connection to the system’s microcontroller.

### 3.9 SENS0374 Sensor

The SENS0374, based on the Bosch BNO055 sensor, is a 9-axis absolute orientation sensor module. It integrates a triaxial accelerometer, gyroscope, and geomagnetic sensor with a 32-bit microcontroller, providing orientation data essential for stable navigation and localization. The module includes an onboard fusion algorithm that combines sensor readings to deliver absolute orientation, minimizing drift over time. The SENS0374 communicates via I2C and SPI, making it flexible for integration with the main controller. This sensor will aid in tracking the robots movement, orientation, and any external forces acting upon it, enhancing its responsiveness in dynamic environments.

### 3.10 SX1280IMLTRT + SKY66122-11

To obtain a reliable connection to the team server, the SX1280IMLTRT RF transceiver with the SKY66122-11 front-endmodule is used.
This implementation has been proven succesful by several teams [3][11].
However, to implement this, a basestation is required and due to the time limitation of this project it is not feasible to design and write firmware for our own network protocol, but these components will be added to the mainboard PCB for future iterations. The communication will instead be done using the wifi on the Raspberry Pi 4.

### 3.11 iC-PX2604 + PX01S 26-30

This wheel encoder comes as a complete module which will be easy to integrate and in combination with the NUCLEO-H723ZG the resolution of the encoder is increased.
Optical wheel encoders is commonly used by teams competing in the SSL competitions.

### 3.12 WSEN-ISDS 6 Axis IMU

The IMU chosen is supplied free of charge from W¨urth electronics. It communicates using I2C or SPI which both are available on the NUCLEO-H723ZG.

### 3.13 Raspberry Pi Camera-module 3

The Raspberry Pi camera-module 3 is chosen because of its seamless integration with the Raspberry Pi 4.
A custom made solenoid would be preferred, but due to time a generic solenoid will be used for starting car engines. Supplied by MDU.

### 3.14 PCB

As some of our components require a custom PCB, three PCBs will be designed. A mainboard, kicker-board and encoder board, the main board will host connectors for the battery, motors, sensors, NUCLEO-H723ZG and pin headers for powering the Raspberry Pi. The mainboard will also host the RF transceiver, IMU and voltage regulators.

## 4 Hardware Architecture

Figure 1 depicting the hardware architecture of the proposed robot.

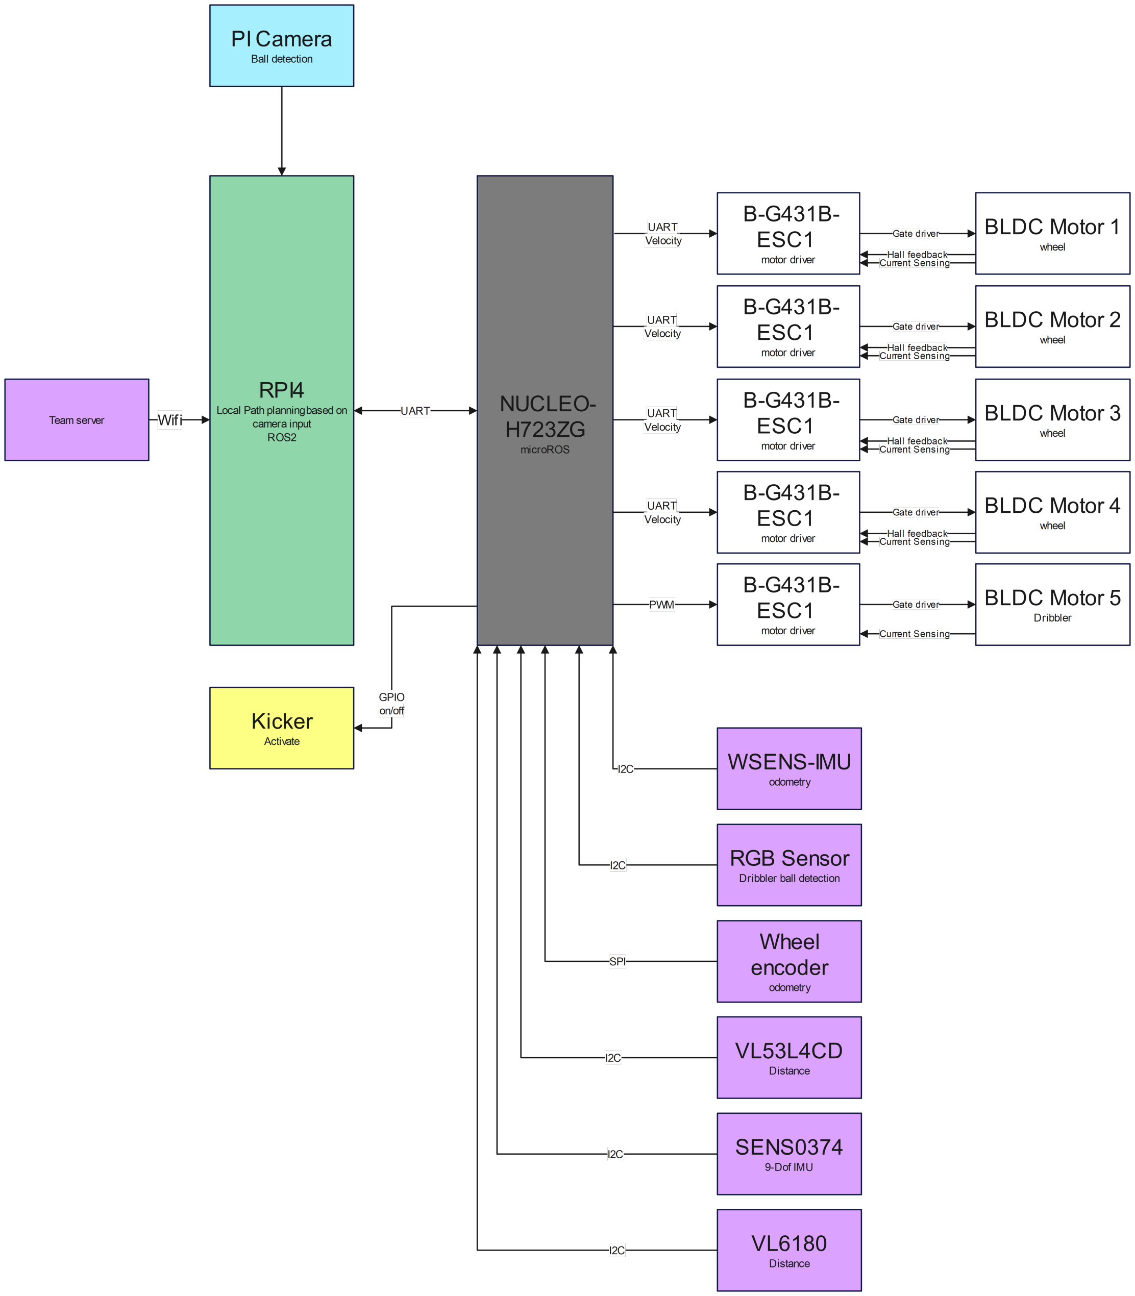
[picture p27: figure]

Figure 1: Hardware Architecture

## References

[1] A. Franca, B. Barros, C. Gomes, C. Silva, C. M. Alves, D. C. Barbosa, D. Xavier, E. Araujo, F. Pereira, L. H. Cavalcanti, M. Asfora, M. Alves, M. Paixao, M. Vasconcelos, M. Vinıcius, J. G. Melo, J. R. Silva, J. Leite, P. H. Santana, P. P. Oliveira, R. Rodrigues, T. Teobaldo, V. Dutra, V. Araujo, and E. Barros, “RobˆoCIn Small Size League Extended Team Description Paper for RoboCup 2024.”
[2] A. Veeraghanta, H. Bryant, S. Zheng, M. MacDougall, S. Guido, and L. Bontkes, “2024 Team Description Paper: The Bots.”
[3] A. Ryll and S. Jut, “Extended Team Description for RoboCup 2020.”
[4] D. R. H. Abiyev, N. Akkaya, T. Yirtici, E. Aytac, G. Burge, S. Abizada, A. Turk, and G. Say, “NEUIslanders Team Description Paper RoboCup 2022.”
[5] Y. Wu, K. Liu, J. Fan, H. Zhang, J. L. Minghe, Q. Li, and J. Li, “Compilation Error Team Description Paper for Small Size League of Robocup 2024.”
[6] A. Rowe, G. Sen Gupta, and S. Demidenko, “Instrumentation and control of a high power BLDC motor for small vehicle applications,” in 2012 IEEE International Instrumentation and Measurement Technology Conference Proceedings. Graz, Austria: IEEE, May 2012, pp. 559–564.
[7] A. Abousaleh, A. Balamurali, B. Blair, R. Cao, M. Charara, L. Chee, J. Coffin, J. Guo, W. Ha, F. Haas, T. Kong,
R. Khan, C. Lee, O. Levy, R. Nedjabat, M. Phung, A. Sidhu, D. Sturn, M. Tong, B. Vasilchikov, K. Wakaba,
N. Zareian, S. Banna, P. Zhou, and Y. B. Zhou, “2024 Team Description Paper: UBC Thunderbots.”
[8] A. Zhao, P. Yu, Z. Huang, N. Shen, J. Yang, J. Yu, Z. Chen, L. Wang, and R. Xiong, “ZJUNlict Extended Team Description Paper.”
[9] N. Ommer, A. Ryll, M. Ratzel, and M. Geiger, “Extended Team Description for RoboCup 2024.”
[10] H. Sato, N. Okamoto, A. Ito, S. Kayaki, T. Nakao, Y. Nishimura, Y. Hara, and R. Yuri, “GreenTea 2024 Team Description Paper.”
[11] H. Barreto, L. E. Horie, E. G. Frese, de Freitas, M. C. Antunes, E. Baldi, and E. H. V. Melo, “RoboIME: Igniting Innovation, Shaping the Future in RoboCup 2024.”

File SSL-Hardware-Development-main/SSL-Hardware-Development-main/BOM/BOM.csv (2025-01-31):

Part name | Quantity | Distributor | Distributor Part Number | Manufacturer | Mfr Part number | Á price | 1 Robot Cost | Lead time | Notes
DF45L024048-A – Brushless DC motor | 4 | https://www.nanotec.com/eu/en/products/1786-df45l024048-a | DF45L024048-A |  |  | 818.4 | 3273.6 | In stock | BLDC motors for the wheels, compact size, light weight, contains hall sensors for encoder feedback Sensored ESC is required if these are used
Hobbywing FPV XRotor 3110 900KV | 1 | https://www.elefun.se/p/prod.aspx?v=65193 | 65193 | https://www.hobbywing.com/ | HW30418005 | 219 | 219 | In stock | BLDC motor for the dribbler
6s 1300mAh -120C - GNB HV XT60 | 1 | https://www.elefun.se/p/prod.aspx?v=63197 | 63197 | http://www.gaonengbattery.com/ | GNB13006S120AHV | 442 | 442 | In stock | Battery
M3 16mm galvanized steel countersunk screw, 100 pack | 1 | https://www.elfa.se/sv/foersaenkt-skruv-foersaenkt-huvud-torx-t10-m3-16mm-paket-med-100-delar-rnd-rnd-610-00397/p/30172632 | 301-72-632 | https://www.elfa.se/sv/manufacturer/rnd/man_rnd | RND 610-00397 | 21.6 | 21.6 | In stock
M3 galvanized steel locking washers, 200 pack | 1 | https://www.elfa.se/sv/lasbricka-m3-foerzinkat-stal-bossard-az-2x6x0/p/30071826 | 300-71-826 | https://www.bossard.com/se-sv/ | AZ 3,2X6X0,4 | 69.7 | 69.7 | In stock
M3 stainless steel nut, 100 pack | 1 | https://www.elfa.se/sv/sexkantsmutter-m3-4mm-rostfritt-stal-rnd-rnd-610-00485/p/30172720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 | 301-72-720 | https://www.elfa.se/sv/manufacturer/rnd/man_rnd | RND 610-00485 | 21.85 | 21.85 | In stock
PHR-6 | 8 | https://www.elfa.se/sv/hylskontakthus-crimpanslutning-uttag-sockel-positioner-2mm-jst-phr/p/14301984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 | 143-01-984 | https://www.elfa.se/sv/manufacturer/jst/man_jst | PHR-6 | 1.07 | 8.56 | In stock | Hall sensor connector for the motor
B6B-PH-K-S | 10 | https://www.elfa.se/sv/stiftlist-enradig-rak-6p-kontaktdon-anslutningsdon-positioner-2mm-jst-b6b-ph/p/14301948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 | 143-01-948 | https://www.elfa.se/sv/manufacturer/jst/man_jst | B6B-PH-K-S | 5.43 | 54.3 | In stock | Hall sensor connector for the motor
VHR-5N | 10 | https://www.elfa.se/sv/crimp-kontakthus-uttag-sockel-positioner-96mm-jst-vhr-5n/p/30021738 | 300-21-738 | https://www.elfa.se/sv/manufacturer/jst/man_jst | VHR-5N | 2.22 | 22.2 | In stock | Motor connectors
X-RING 3.63X2.62/NBR70 | 100 | https://webbshop.teknikprodukter.se/x-ring-3-63x2-62-nbr70-2111395n70 | 2111395N70 |  |  | 6.2 | 620 | in stock | Price dependent on the amount you buy
SENS | 1 | https://www.mouser.se/ProductDetail/DFRobot/SEN0374?qs=81r%252BiQLm7BRSXhV57X59YA%3D%3D | 426-SEN0374 | https://www.mouser.se/manufacturer/dfrobot/ | SEN0374 | 191.48 | 191.48 | 4 left in stock | 9Dof IMU
Raspberry Pi RTC | 1 | https://www.mouser.se/ProductDetail/Seeed-Studio/103030277?qs=0lSvoLzn4L8soh3xbH07wQ%3D%3D | 713-103030277 | https://www.mouser.se/manufacturer/seeed-studio/ | 103030277 | 1 | 47.61 | In stock
LT3751 | 2 | https://www.mouser.se/ProductDetail/Analog-Devices/LT3751IFEPBF?qs=hVkxg5c3xu8wGIOCrD9eEw%3D%3D | 584-LT3751IFE#PBF | https://www.mouser.se/manufacturer/analog-devices/ | LT3751IFE#PBF | 147.09 | 294.18 | In stock | Capacitor charging controller for kicker
LM74500QDDFRQ1 | 2 | https://www.mouser.se/ProductDetail/Texas-Instruments/LM74500QDDFRQ1?qs=stqOd1AaK7%252BDaolIEn1S7g%3D%3D | 595-LM74500QDDFRQ1 | https://www.mouser.se/manufacturer/texas-instruments/ | LM74500QDDFRQ1 | 16.45 | 32.9 | In stock | Reverse polarity protection
PSMN6R7-40MLDX | 2 | https://www.mouser.se/ProductDetail/Nexperia/PSMN6R7-40MLDX?qs=XeJtXLiO41T0U8eRNXd8kw%3D%3D | 771-PSMN6R7-40MLDX | https://www.mouser.se/manufacturer/nexperia/ | PSMN6R7-40MLDX | 5.77 | 11.54 | In stock | Mosfet used with the reverse polarity protection component
NUCLEO-H723ZG | 1 | https://www.mouser.se/ProductDetail/511-NUCLEO-H723ZG | 511-NUCLEO-H723ZG | https://www.mouser.se/manufacturer/stmicroelectronics/ | NUCLEO-H723ZG | 322.58 | 322.58 | In stock | If we do not develop our own pcb this microcontroller can be used instead of the ESP32 microcontroll- Er, ADC, communication, supports micro ros
SX1280IMLTRT | 1 | https://www.mouser.se/ProductDetail/Semtech/SX1280IMLTRT?qs=5aG0NVq1C4xuoq8G6ZzdxQ%3D%3D | 947-SX1280IMLTRT | https://www.mouser.se/manufacturer/semtech/ | SX1280IMLTRT | 75.44 | 75.44 | In stock | RF Transceiver Long range 2.4 GHz Wireless Transceiver
SKY66122-11 | 1 | https://www.mouser.se/ProductDetail/Skyworks-Solutions-Inc/SKY66122-11?qs=stqOd1AaK7%2F9zH4JdBCX2A%3D%3D | 873-SKY66122-11 | https://www.mouser.se/manufacturer/skyworks-solutions/ | SKY66122-11 | 40.48 | 40.48 | In stock | RF Front End OFDM, 863 to 928 MHz, Wi-SUN, FEM
B-G431B-ESC1 | 5 | https://www.mouser.se/ProductDetail/511-B-G431B-ESC1 | 511-B-G431B-ESC1 | https://www.mouser.se/manufacturer/stmicroelectronics/ | B-G431B-ESC1 | 208.96 | 1044.8 | In stock | Datasheet
VS-5EWH06FN-M3 | 4 | https://www.mouser.se/ProductDetail/Vishay-Semiconductors/VS-5EWH06FN-M3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 | 78-VS-5EWH06FN-M3 | https://www.mouser.se/manufacturer/vishaysemiconductors/ | VS-5EWH06FN-M3 | 10 | 48 | In stock | Kicker circuit
SMAJ20A | 3 | https://www.mouser.se/ProductDetail/Littelfuse/SMAJ20A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 | 576-SMAJ20A | https://www.mouser.se/manufacturer/littelfuse/ | SMAJ20A | 4 | 28 | In stock | Kicker circuit
TLP3910(C20-TP | 3 | https://www.mouser.se/ProductDetail/Toshiba/TLP3910C20-TPE?qs=TuK3vfAjtkUvVtweYOqjVw== | 757-TLP3910C20-TPE | https://www.mouser.se/manufacturer/toshiba-semiconductors/ | TLP3910(C20-TP | 36 | 46 | In stock | Kicker circuit
ECW-FD2J823KQ | 3 | https://www.mouser.se/ProductDetail/Panasonic/ECW-FD2J823KQ?qs=7EBvPakHacV3NgMNuq1u4w== | 667-ECW-FD2J823KQ | https://www.mouser.se/manufacturer/panasonicec/ | ECW-FD2J823KQ | 6 | 64 | In stock | Kicker circuit
CKG57NX7R2J474M500JH | 3 | https://www.mouser.se/ProductDetail/TDK/CKG57NX7R2J474M500JH?qs=NRhsANhppD%2BAmXDR5rVERg== | 810-CKG57NX7R2J474M | https://www.mouser.se/manufacturer/tdk/ | CKG57NX7R2J474M500JH | 46 | 58 | In stock | Kicker circuit
US1M | 3 | https://www.mouser.se/ProductDetail/Taiwan-Semiconductor/US1M?qs=tHU/lV7kTyQtvhnvJdnZJw== | 821-US1M | https://www.mouser.se/manufacturer/taiwan-semiconductor/ | US1M | 3 | 11 | In stock | Kicker circuit
FQB4N80TM | 3 | https://www.mouser.se/ProductDetail/onsemi-Fairchild/FQB4N80TM?qs=FOlmdCx%2BAA3dgdfgWff8ng== | 512-FQB4N80TM | https://www.mouser.se/manufacturer/fairchild-semiconductor/ | FQB4N80TM | 25 | 7 | In stock | Kicker circuit
IKB40N65ES5ATMA1 | 2 | https://www.mouser.se/ProductDetail/Infineon-Technologies/IKB40N65ES5ATMA1?qs=MLItCLRbWsxz7jtfFbVz2w%3D%3D | 726-IKB40N65ES5ATMA1 |  | IKB40N65ES5ATMA1 | 43.93 | 87.86 |  | Kicker Circuit
195207-231 | 1 | https://www.mouser.se/ProductDetail/Ledex/195207-231?qs=byeeYqUIh0N3hSxJ8HFfVg== | 906-195207-231 | https://www.mouser.se/manufacturer/ledex/ | 195207-231 | 426 | 19 | In stock | Kicker circuit
Wheel hub 4mm | 4 | https://www.electrokit.com/axelnav-med-klamfaste-4mm | 41020172 | https://www.gobilda.com/ | 1309-0016-0004 | 139 | 556 | in stock | Kicker circuit
Raspberry Pi 4 Model B/8GB | 1 | https://www.electrokit.com/raspberry-pi-4-model-b/8gb | 41017664 - Raspberry Pi | https://www.raspberrypi.com/ |  | 979 | 979 | In stock | Can be substituted with Raspberry Pi 4 Model B/4GB
Raspberry Pi Kameramodul 3 | 1 | https://www.electrokit.com/raspberry-pi-kameramodul-3-12mp-75 | 41020240 - Raspberry Pi | https://www.raspberrypi.com/ |  | 369 | 369 | In stock | Needs to be ordered with Raspberry Pi 4 Model B/8GB or Raspberry Pi 4 Model B/4GB
Bearings 5mm | 6 | https://www.electrokit.com/kullager-5mm | 41019266 |  |  | 15 | 90 | In stock | for dribbler assembly.
M3 threaded inserts 3mm, 50 pack | 1 | https://www.electrokit.com/ganginsats-m3-x-3mm-50-pack | 41018554 |  |  | 95 | 95 | In stock
APDS-9960 | 1 |  | 41013512 – Sparkfun | https://www.sparkfun.com/ | APDS-9960 | 199 | 199 | In stock | Chosen by UdeA, RGB sensor
TOF400C-VL53L1 | 1 | https://www.amazon.com/Teyleten-Robot-TOF400C-VL53L1X-Distance/dp/B0CLDKMGZR |  | https://www.mouser.se/manufacturer/stmicroelectronics/ | VL53L1CBV0FY/1 | 176.32 | 176.32 | In stock | Chosen by UdeA, could not find from another seller
VL6180 TOF | 1 | https://www.tinytronics.nl/en/sensors/distance/vl6180-time-of-flight-tof-distance-sensor |  | https://www.st.com/en/imaging-and-photonics-solutions/vl6180.html | VL6180 | 33 | 33 | In stock | Chosen by UdeA, could not find from another seller
XT60PW-M | 1 | https://www.tme.eu/se/details/xt60pw-m/dc-kontaktdon/amass/ | XT60PW-M | https://www.tme.eu/se/katalog/p,amass_1260/ | XT60PW-M | 11.21 | 11.21 | In stock | XT60 PCB connector
2-post pillow block, 32mm bore | 4 | https://eu.robotshop.com/products/servocity-1-side-2-post-pillow-block-32mm-bore | RP-Sct-2151 | https://www.servocity.com/ | 1602-0032 | 172.29 | 689.16 | On demand, 1 month delivery time | For extra support for the wheels, compatible with chosen hub.
B5P-VH | 10 | https://se.farnell.com/jst-japan-solderless-terminals/b5p-vh-lf-sn/connector-header-5pos-3-96mm-1row/dp/2399164 | JST (JAPAN SOLDERLESS TERMINALS) B5P-VH(LF)(SN) | https://se.farnell.com/b/jst-japan-solderless-terminals | B5P-VH(LF)(SN) | 5.21 | 52.1 | In stock | Motor connectors
OFFERT finns för nedanstående, se bifogad fil
OFFERT – BROADCOM AEDB-9140-A13 | 8 | https://uk.farnell.com/broadcom-limited/aedb-9140-a13/encoder-3channel-500cpr-8mm/dp/1161087 | BROADCOM AEDB-9140-A13 | https://uk.farnell.com/b/broadcom | AEDB-9140-A13 | 309 | 2472 | In stock | Offert från farnell med studentrabatt
 |  |  |  |  |  |  | 12904.47

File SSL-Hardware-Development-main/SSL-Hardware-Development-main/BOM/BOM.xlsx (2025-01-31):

Powertrain and Electronics
Ranking | Part name | Quantity | Distributor | Distributor Part Number | Manufacturer | Mfr Part number | Á price | Estimated cost | Lead time | Notes
Motor Wheel
1 | DF45L024048-A – Brushless DC motor | 4 | Nanotec (https://www.nanotec.com/eu/en/products/1786-df45l024048-a) | DF45L024048-A |  |  | 818.40 | 3273.60 | In stock | BLDC motors for the wheels, compact size, light weight, contains hall sensors for encoder feedback Sensored ESC is required if these are used
UdeA | MN5208 Navigator Type UAV Multi-Motor KV340 | 4 | T-motor (https://store.tmotor.com/product/mn5208-motor-navigator-type.html) | MN5208 |  |  | 1027.32 | 4109.28 | In stock | Motors similar to the one UdeA will use. Terrible torque at low speed, international shipping. Expensive compared to the DF45L024048-A
2 | Turnigy Multistar 4225-610Kv 16Pole Multi-Rotor Outrunner | 4 | HobbyKing (https://hobbyking.com/en_us/turnigy-multistar-4225-610kv-16pole-multi-rotor-outrunner.html) | 9392000008 |  |  | 297.00 | 1188.00 | In stock | Wheel BLDC Small form factor + low weight 86g Balanced RPM/V (610kV): Good tradeoff between speed and torque It provides good torque at low speeds which is needed for fast acceleration 16 poles, which gives pretty good control
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

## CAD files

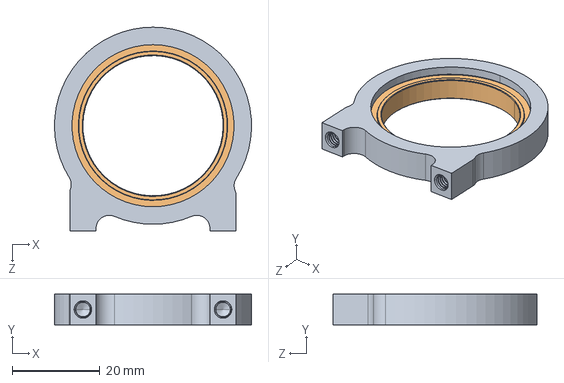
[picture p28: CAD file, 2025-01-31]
SSL-Hardware-Development-main/SSL-Hardware-Development-main/3D_Models/CAD_Files/Purchased_parts/1602-0032-0032 assembly.STEP
45.0 x 7.00 x 46.5 mm

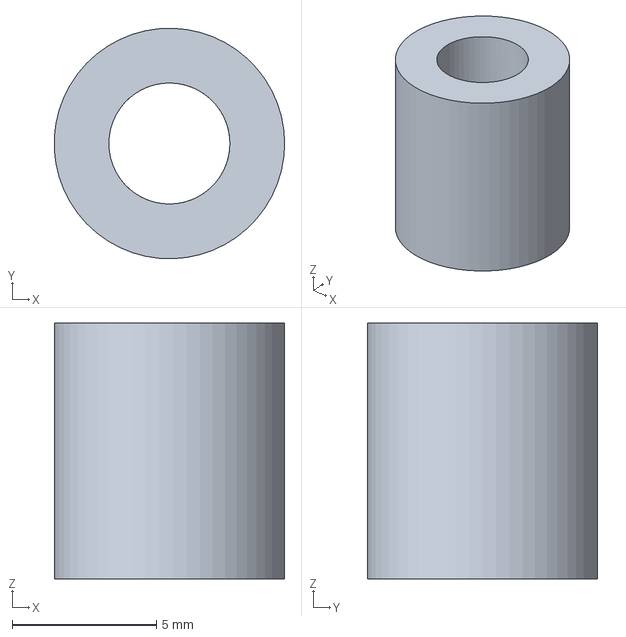
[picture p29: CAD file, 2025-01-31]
SSL-Hardware-Development-main/SSL-Hardware-Development-main/3D_Models/CAD_Files/step/offset_mainboard.step
7.99 x 8.00 x 8.88 mm

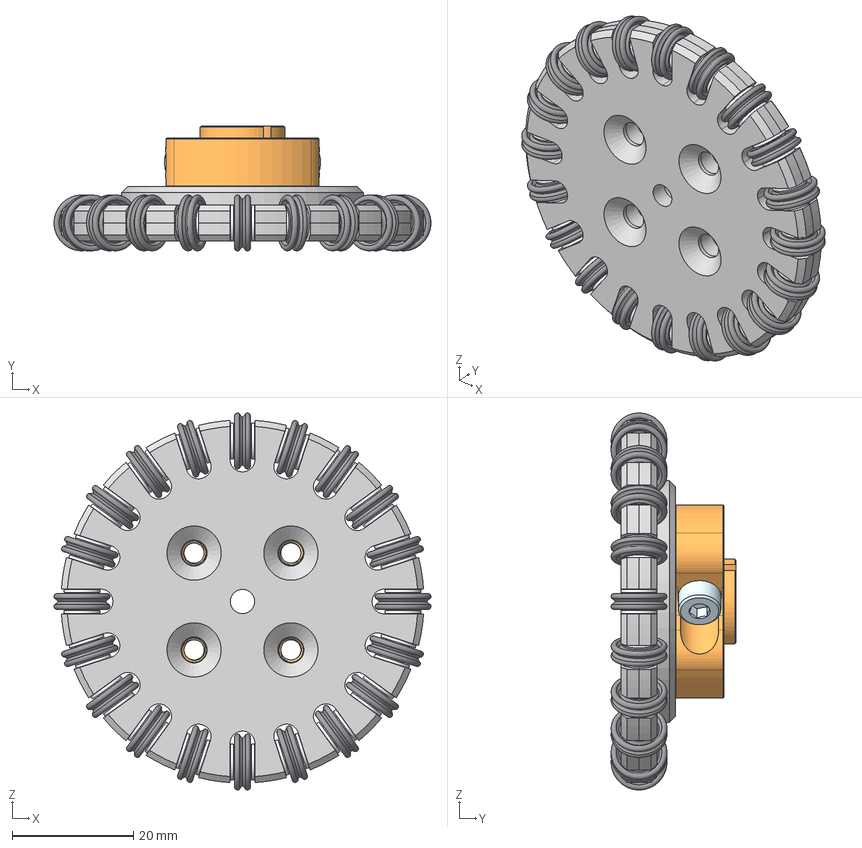
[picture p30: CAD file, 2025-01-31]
SSL-Hardware-Development-main/SSL-Hardware-Development-main/3D_Models/CAD_Files/step/Wheel_assembly.step
62.3 x 20.6 x 62.3 mm
Wheel x 2
x-ring x 20
TPE_bearing x 20
nylon_washer x 40
Parallel pin 2.5 x 8 x 20
Wheel_standoff
2800-0004-0014_90128A207 x 2

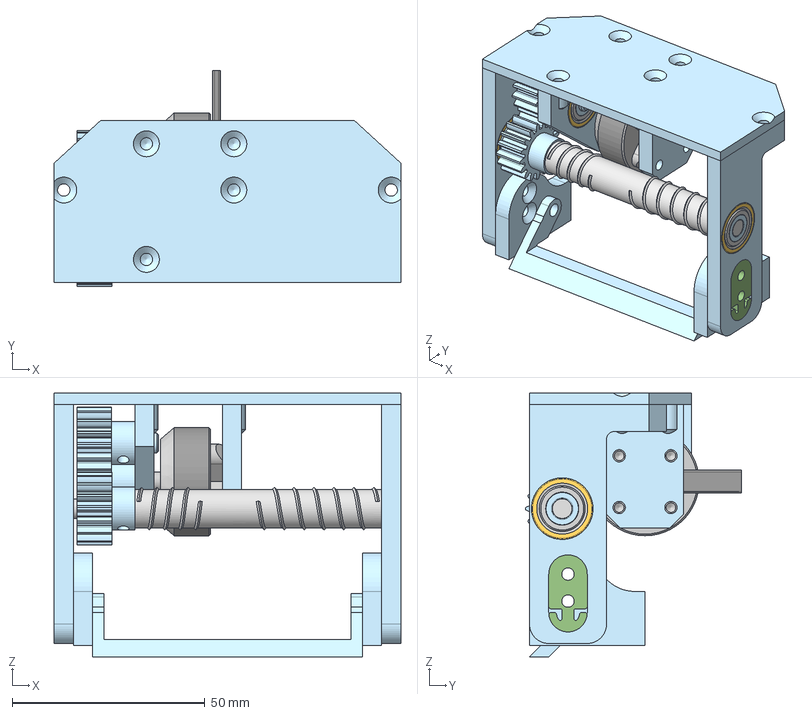
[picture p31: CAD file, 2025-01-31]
SSL-Hardware-Development-main/SSL-Hardware-Development-main/3D_Models/CAD_Files/step/Dribbler_Assembly.step
90.1 x 56.0 x 68.5 mm
Dribbler_mount x 2
Catch_bar _v3
dribbler_dampener x 2
Roller
Spur 1M 17T x 3
skf_bearing_625-z_2_1 x 16
pin_3dprint
Dribbler_bearing_holder
dribbler_motor

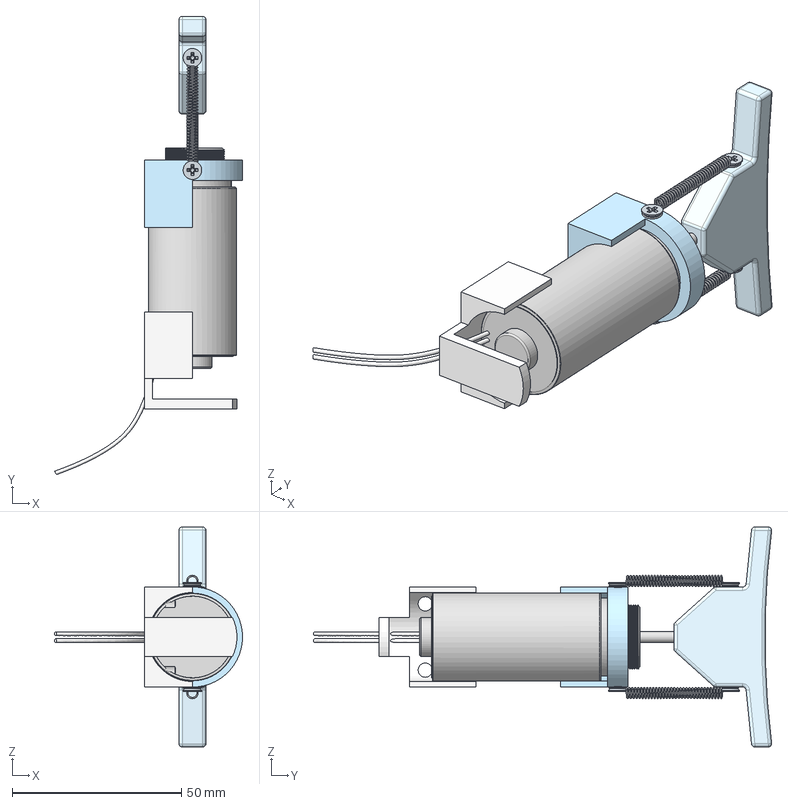
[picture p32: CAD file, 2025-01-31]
SSL-Hardware-Development-main/SSL-Hardware-Development-main/3D_Models/CAD_Files/step/Kicker_Assembly.step
55.6 x 135.4 x 65.0 mm
PH Countersunk flat head screw M3x0.5 x 6 x 6

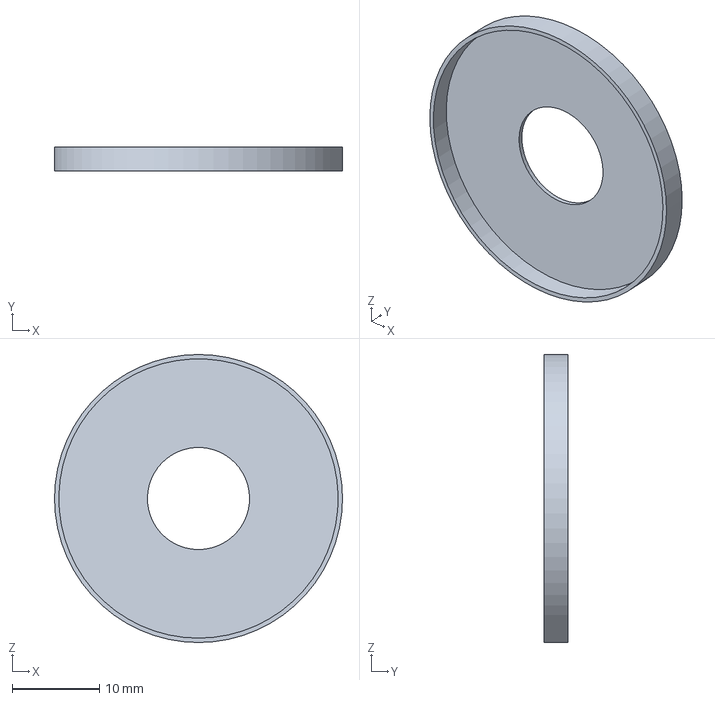
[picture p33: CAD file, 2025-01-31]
SSL-Hardware-Development-main/SSL-Hardware-Development-main/3D_Models/CAD_Files/step/Encoder_backing.step
33.0 x 2.80 x 33.0 mm

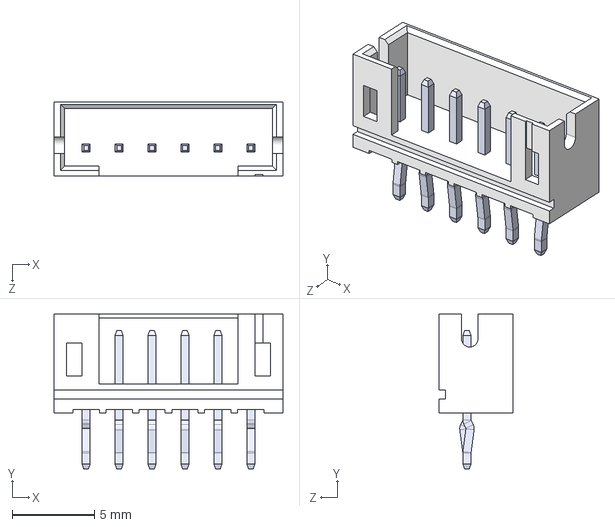
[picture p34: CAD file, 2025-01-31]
SSL-Hardware-Development-main/SSL-Hardware-Development-main/Circuits/Components/B6B-PH-K-S/B6B-PH-K-S--3DModel-STEP-56544.STEP
13.9 x 9.40 x 4.50 mm
pin x 6

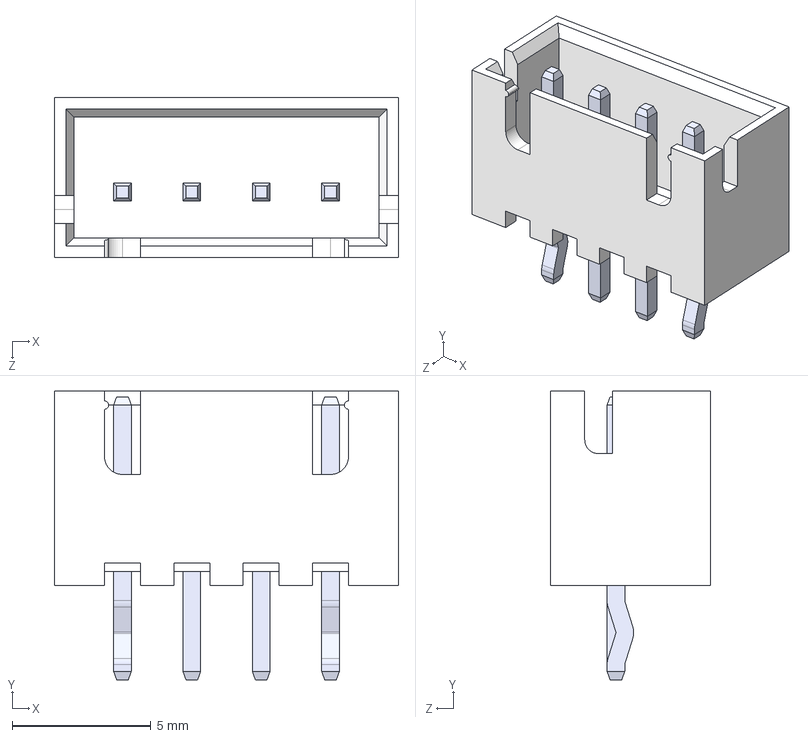
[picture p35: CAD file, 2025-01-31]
SSL-Hardware-Development-main/SSL-Hardware-Development-main/Circuits/Components/JST-XH 4A 2.54 mm pitch/B4B-XH-A--3DModel-STEP-56544.STEP
12.4 x 10.4 x 5.75 mm

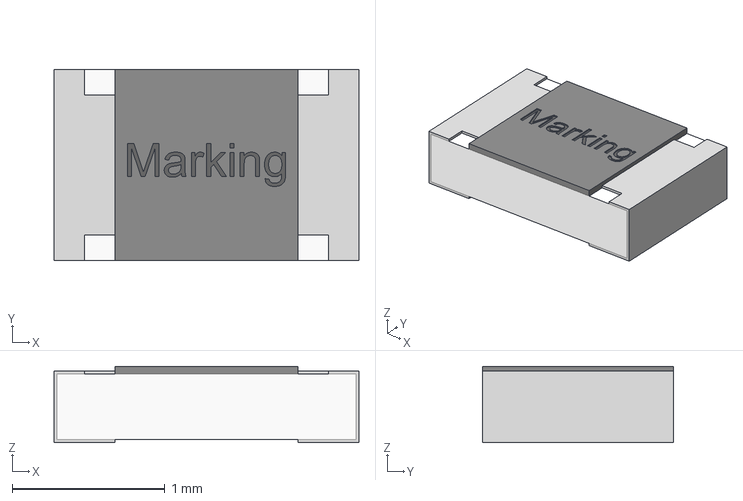
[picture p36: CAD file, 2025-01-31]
SSL-Hardware-Development-main/SSL-Hardware-Development-main/Circuits/Components/WE_560112120004_Libraries/IGS_WRIS-RSKS_0805 (rev1).igs
2.00 x 1.25 x 0.5 mm

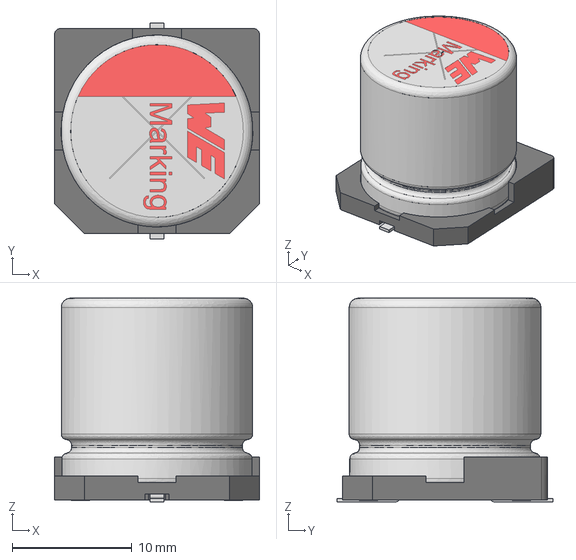
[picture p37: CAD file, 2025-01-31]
SSL-Hardware-Development-main/SSL-Hardware-Development-main/Circuits/Components/WE_865060663013_Libraries/IGS_WCAP-ASLL_16x17x6 (rev1).igs
17.1 x 18.0 x 17.0 mm

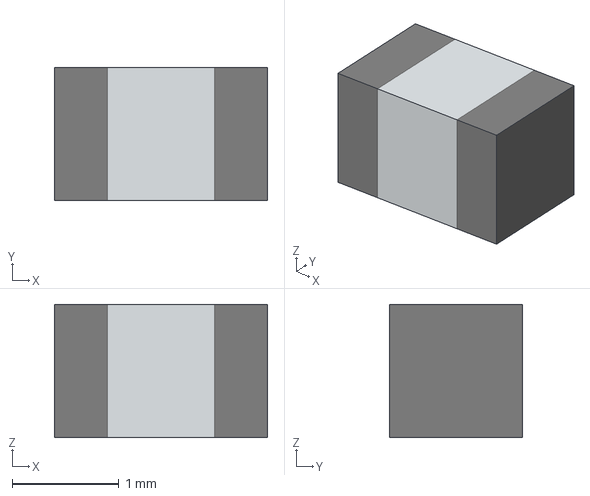
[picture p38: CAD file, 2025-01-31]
SSL-Hardware-Development-main/SSL-Hardware-Development-main/Circuits/Components/WE_885012107006_Libraries/IGS_MLCC_WACP-CSGP_0805 (rev1).igs
2.00 x 1.25 x 1.25 mm

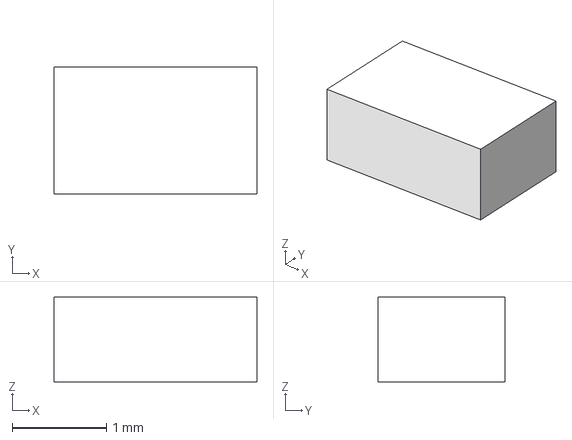
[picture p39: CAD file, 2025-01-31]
SSL-Hardware-Development-main/SSL-Hardware-Development-main/Circuits/Components/WE_885012207098_Libraries/IGS_WCAP-CSGP_0805_ 2.0x1.25x0.8x0 (rev1).igs
2.15 x 1.35 x 0.9 mm

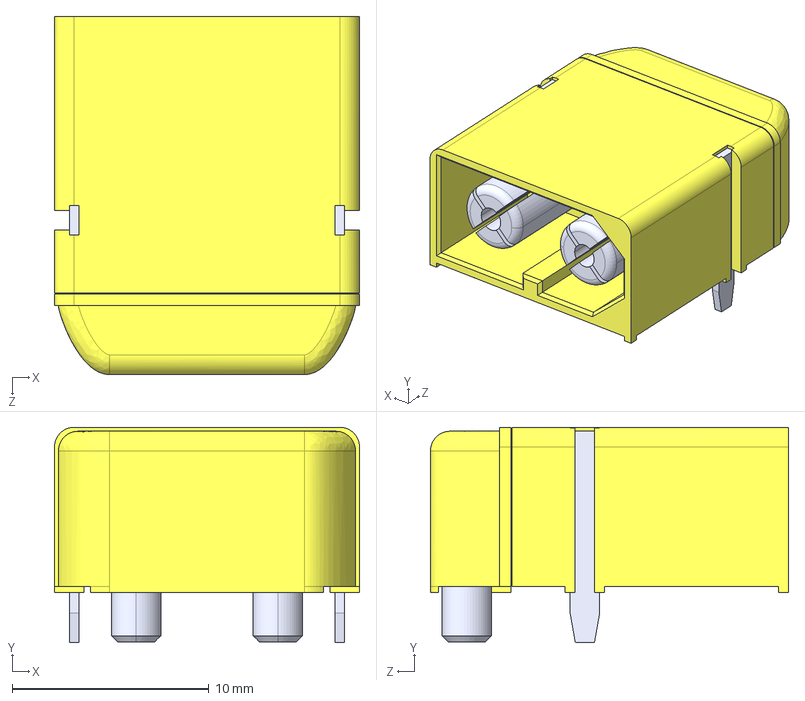
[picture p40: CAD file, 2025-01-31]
SSL-Hardware-Development-main/SSL-Hardware-Development-main/Circuits/Components/XT60PW-M/XT60PW-M--3DModel-STEP-269445.STEP
15.5 x 11.0 x 18.2 mm

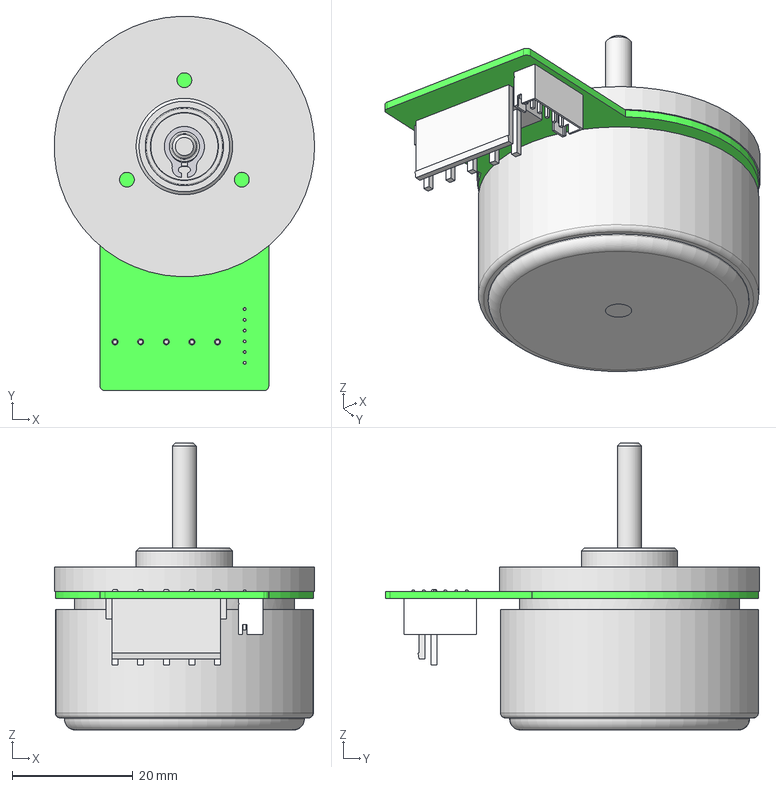
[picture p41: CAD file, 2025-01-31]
SSL-Hardware-Development-main/SSL-Hardware-Development-main/3D_Models/CAD_Files/Purchased_parts/DF45L024048-A.stp
43.2 x 62.1 x 47.6 mm
Frontcap-DF45L
PCB-DF45-A
Glocke-DF45L
Welle-DF45L
Innenteil-DF45L
_R-1350ZZ_ir x 2
_R-1350ZZ_cage x 2
_R-1350ZZ_ball x 16
_R-1350ZZ_or x 2
_R-1350ZZ_shield x 4
DIN 471 <= 9mm 5 x 0,6
Connector 1
Connector 2

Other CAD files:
SSL-Hardware-Development-main/SSL-Hardware-Development-main/Circuits/Mainboard/Mainboard/Unnamed-Mainboard.obj
SSL-Hardware-Development-main/SSL-Hardware-Development-main/3D_Models/CAD_Files/step/Roller.step
SSL-Hardware-Development-main/SSL-Hardware-Development-main/3D_Models/CAD_Files/Purchased_parts/traxxas_6490x_17t_m1_pinion.step
SSL-Hardware-Development-main/SSL-Hardware-Development-main/3D_Models/CAD_Files/Purchased_parts/195207-228.stp
SSL-Hardware-Development-main/SSL-Hardware-Development-main/3D_Models/CAD_Files/Purchased_parts/skf_bearing_625-z_2.stp
SSL-Hardware-Development-main/SSL-Hardware-Development-main/3D_Models/CAD_Files/step/Base_plate.step
SSL-Hardware-Development-main/SSL-Hardware-Development-main/3D_Models/CAD_Files/step/Battery.step
SSL-Hardware-Development-main/SSL-Hardware-Development-main/3D_Models/CAD_Files/step/Battery_mount_bottom.step
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

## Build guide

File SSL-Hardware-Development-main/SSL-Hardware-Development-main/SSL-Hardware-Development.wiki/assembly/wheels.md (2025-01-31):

# Wheel assembly

## Wheels

### Components

| Item | Amount |
| :--- | ---: |
| Wheel front | 1 |
| Wheel back | 1 |
| Steel pin | 20 |
| X-ring | 20 |
| TPE bearing | 20 |
| Nylon washer | 40 |

### Assembly Instructions
Step-by-step instructions for assembling the wheel. Recommended tools: Tweezers, cylindrical base.
1. Items:


2. Place a wheel back onto a cylindrical base with clearance for the sub wheel slots.


3. Thread the bearing onto the steel pin.


4. Place the X-ring onto the bearing.
PXL_20241213_111629265 MP

5. Place 1 nylon washer on each side of the X-ring.


6. Carefully place the subwheel assembly into one of the slots, ensuring that the washers stay in line with the X-ring.


7. Repeat this process for all 20 subwheels. This needs to be done methodically so the already placed sub wheels don't fall off, since there is nothing keeping them in place.
8. Once all 20 sub wheels are in place, line up the holes of the wheel front with the holes of the wheel back, and press into place. There will probably be resistance from the nylon washers, so gently push on the washers from the side until the front and back can be pushed together.
9. While holding onto the wheel to keep them together, screw the wheel together with the hub to ensure that the sub wheels are securely in place.



## Drive assembly
### Components

| Item | Amount |
| :---  | ---: |
| Wheel with hub | 1 |
| Pillow block | 1 |
| Wheel motor | 1 |
| Lagerbock | 1 |
| M3 Screw | 5 |
| M4 Screw | 2 |

Optionally for encoder sensor:

| Item | Amount |
| :--- | ---: |
| Encoder disk | 1 |
| Encoder backing | 1 |
| Encoder holder with nut | 20 |

1x Encoder disk

1x Encoder backing

1x Encoder holder with nut

### Assembly Instructions

Step-by-step instructions for assembling the wheel. Needed tools: depending on the screw, we use torx.

1. Items: 


2. Place the lagerblock so that the holes line up with the motor holes.


3. Screw in 3 short M3 screws.


4. Place the pillowblock on top of the lagerbock.


5. Take the motor and pillowblock and place it in it's location on top of the bottom plate. Then slide the wheel onto the motor axis.


6. Screw the lagerbock loosely into place. Don't fasten the pillow block.


7. Before tightening the pillow block in place, make sure the wheel is fully on the motor axis and then tighten the hub screws to ensure that the wheels stay on.


8. The pillow block can now be fastened and the lagerbock screws can also be fully fastened.


9. Do the same for the 3 remaining drive assemblies.


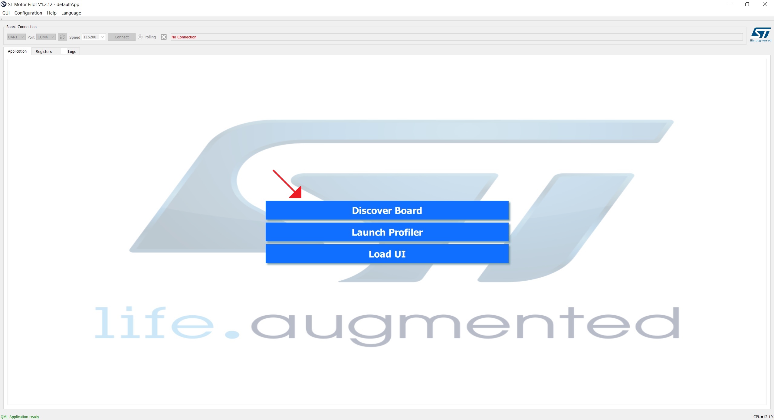
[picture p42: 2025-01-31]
foc-code-main/foc-code-main/instruction_pictures/mc_workbench_motor_pilot_default_gui.jpg

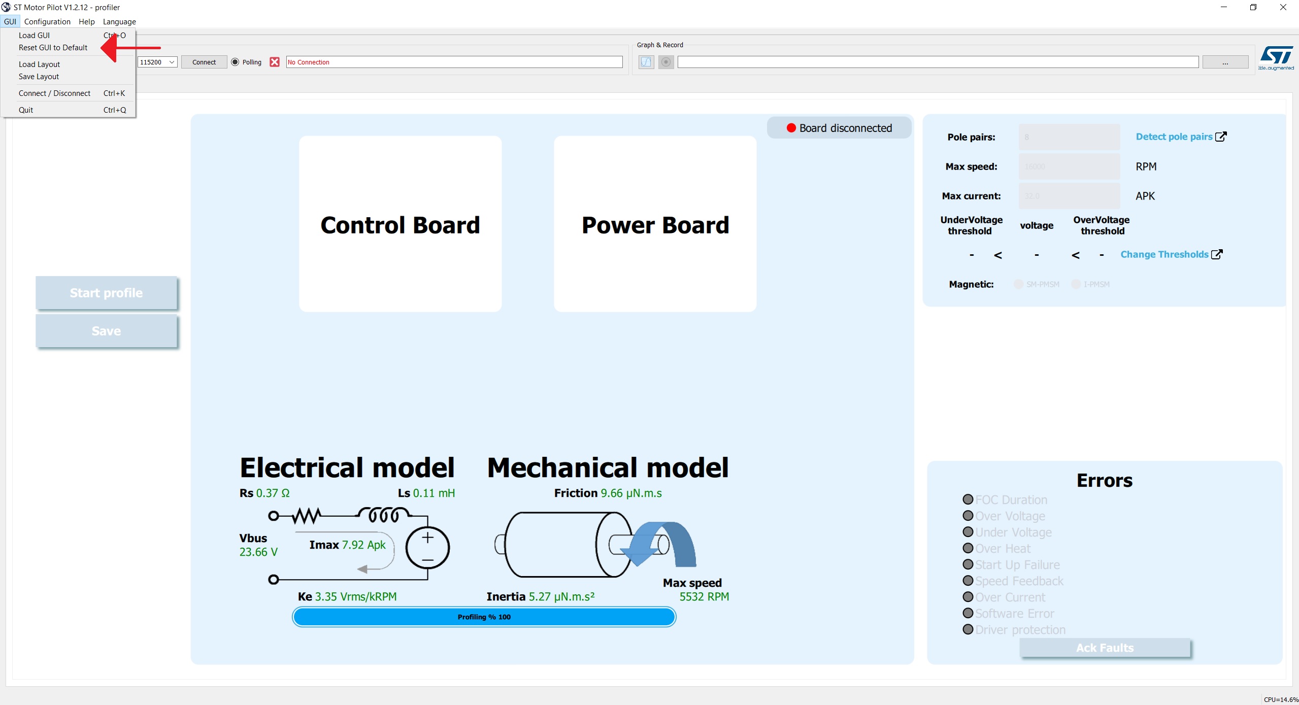
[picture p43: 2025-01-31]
foc-code-main/foc-code-main/instruction_pictures/mc_workbench_motor_pilot_reset_gui_to_default.jpg

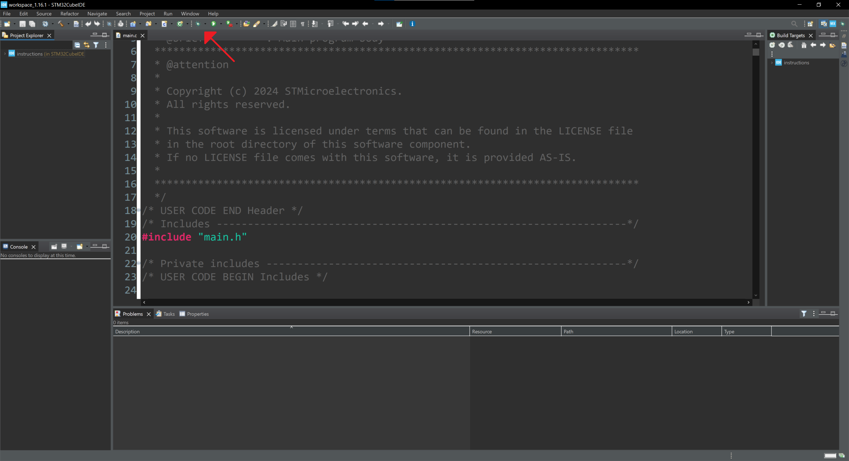
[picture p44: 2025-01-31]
foc-code-main/foc-code-main/instruction_pictures/stm32cubeide_flash_the_code.jpg

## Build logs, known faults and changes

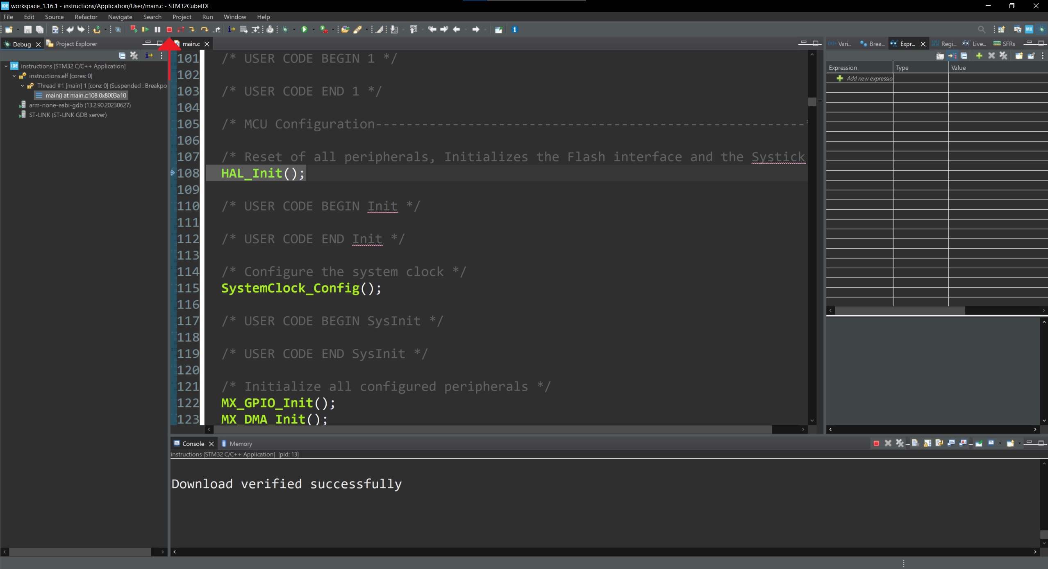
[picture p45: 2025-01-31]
foc-code-main/foc-code-main/instruction_pictures/stm32cubeide_terminate_debugger.jpg

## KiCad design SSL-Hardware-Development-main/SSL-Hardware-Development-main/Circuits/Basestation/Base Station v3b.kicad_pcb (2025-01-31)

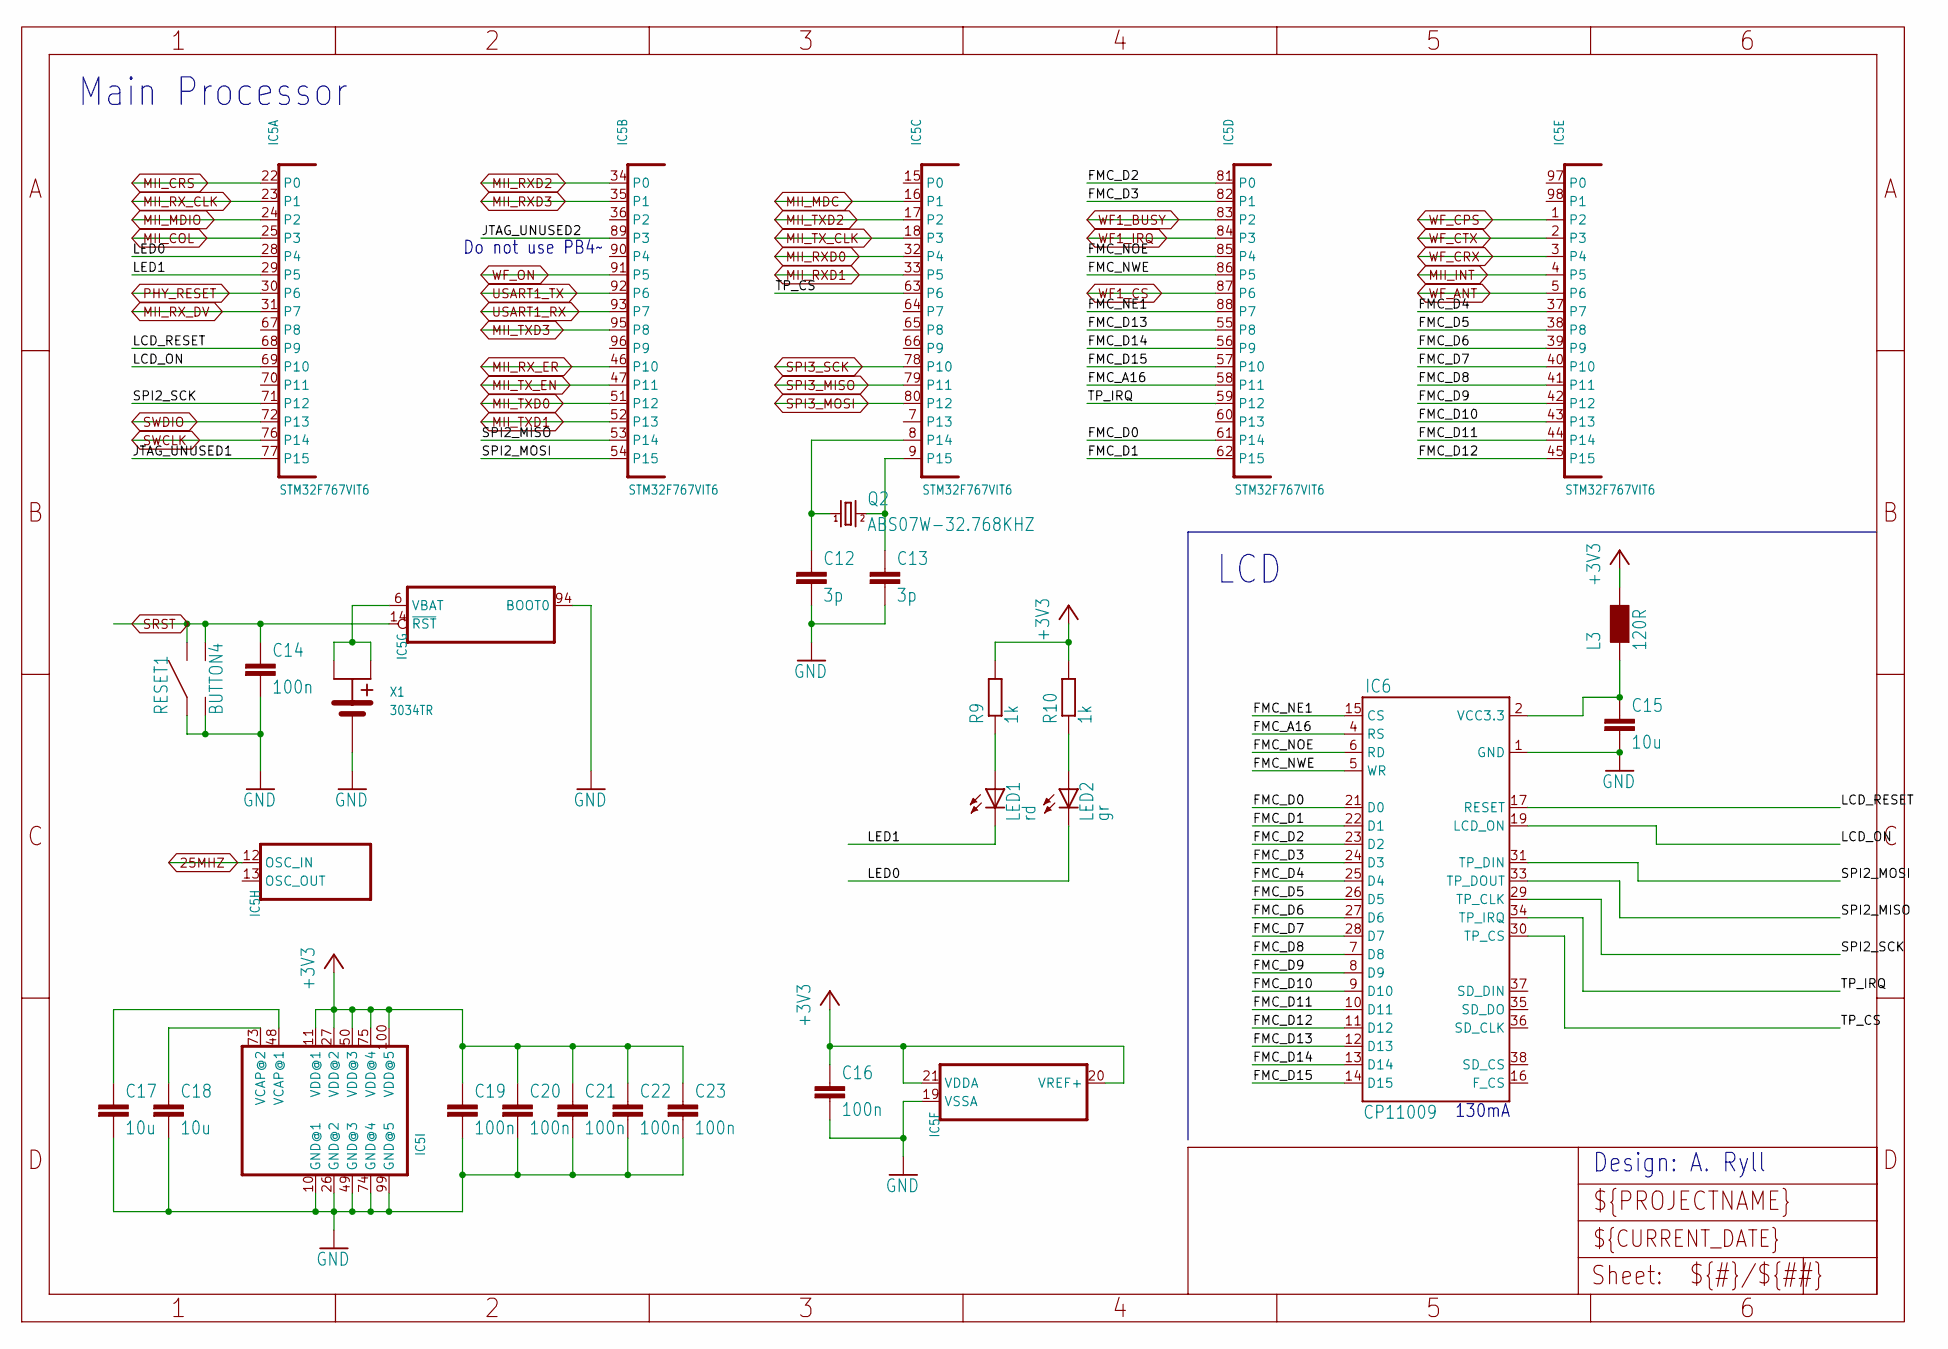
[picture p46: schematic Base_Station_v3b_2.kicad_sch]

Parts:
C12, C13: 3p; C0603
C14, C16, C19, C20, C21, C22, C23: 100n; C0603
C15, C17, C18: 10u; C0603
IC5: STM32F767VIT6; LQFP100-ST
IC6: CP11009; CP11009-THX
L3: 120R; 0603
LED1: rd; CHIP-LED0603
LED2: gr; CHIP-LED0603
Q2: ABS07W-32.768KHZ; CRYSTAL-07W
R9, R10: 1k; R0603
RESET1: BUTTON4
X1: 3034TR; CR2025

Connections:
25MHZ: IC5.12 (OSC_IN); also elsewhere on the board
+3V3: C16.1, C19.1, C20.1, C21.1, C22.1, C23.1, IC5.11 (VDD@1), IC5.20 (VREF+), IC5.21 (VDDA), IC5.27 (VDD@2), IC5.50 (VDD@3), IC5.75 (VDD@4), IC5.100 (VDD@5), L3.2, R9.2, R10.2; also elsewhere on the board
FMC_A16: IC5.58 (P11), IC6.4 (RS)
FMC_D0: IC5.61 (P14), IC6.21 (D0)
FMC_D1: IC5.62 (P15), IC6.22 (D1)
FMC_D2: IC5.81 (P0), IC6.23 (D2)
FMC_D3: IC5.82 (P1), IC6.24 (D3)
FMC_D4: IC5.37 (P7), IC6.25 (D4)
FMC_D5: IC5.38 (P8), IC6.26 (D5)
FMC_D6: IC5.39 (P9), IC6.27 (D6)
FMC_D7: IC5.40 (P10), IC6.28 (D7)
FMC_D8: IC5.41 (P11), IC6.7 (D8)
FMC_D9: IC5.42 (P12), IC6.8 (D9)
FMC_D10: IC5.43 (P13), IC6.9 (D10)
FMC_D11: IC5.44 (P14), IC6.10 (D11)
FMC_D12: IC5.45 (P15), IC6.11 (D12)
FMC_D13: IC5.55 (P8), IC6.12 (D13)
FMC_D14: IC5.56 (P9), IC6.13 (D14)
FMC_D15: IC5.57 (P10), IC6.14 (D15)
FMC_NE1: IC5.88 (P7), IC6.15 (CS)
FMC_NOE: IC5.85 (P4), IC6.6 (RD)
FMC_NWE: IC5.86 (P5), IC6.5 (WR)
GND: C12.2, C13.2, C14.2, C15.2, C16.2, C17.2, C18.2, C19.2, C20.2, C21.2, C22.2, C23.2, IC5.10 (GND@1), IC5.19 (VSSA), IC5.26 (GND@2), IC5.49 (GND@3), IC5.74 (GND@4), IC5.94 (BOOT0), IC5.99 (GND@5), IC6.1 (GND), RESET1.1, RESET1.2, X1.GND; also elsewhere on the board
JTAG_UNUSED1: IC5.77 (P15)
JTAG_UNUSED2: IC5.89 (P3)
LCD_ON: IC5.69 (P10), IC6.19 (LCD_ON)
LCD_RESET: IC5.68 (P9), IC6.17 (RESET)
LED0: IC5.28 (P4), LED2.C
LED1: IC5.29 (P5), LED1.C
MII_COL: IC5.25 (P3); also elsewhere on the board
MII_CRS: IC5.22 (P0); also elsewhere on the board
MII_INT: IC5.4 (P5); also elsewhere on the board
MII_MDC: IC5.16 (P1); also elsewhere on the board
MII_MDIO: IC5.24 (P2); also elsewhere on the board
MII_RXD0: IC5.32 (P4); also elsewhere on the board
MII_RXD1: IC5.33 (P5); also elsewhere on the board
MII_RXD2: IC5.34 (P0); also elsewhere on the board
MII_RXD3: IC5.35 (P1); also elsewhere on the board
MII_RX_CLK: IC5.23 (P1); also elsewhere on the board
MII_RX_DV: IC5.31 (P7); also elsewhere on the board
MII_RX_ER: IC5.46 (P10); also elsewhere on the board
MII_TXD0: IC5.51 (P12); also elsewhere on the board
MII_TXD1: IC5.52 (P13); also elsewhere on the board
MII_TXD2: IC5.17 (P2); also elsewhere on the board
MII_TXD3: IC5.95 (P8); also elsewhere on the board
MII_TX_CLK: IC5.18 (P3); also elsewhere on the board
MII_TX_EN: IC5.47 (P11); also elsewhere on the board
unnamed: C18.1, IC5.73 (VCAP@2)
unnamed: C17.1, IC5.48 (VCAP@1)
unnamed: LED2.A, R10.1
unnamed: LED1.A, R9.1
unnamed: C15.1, IC6.2 (VCC3.3), L3.1
OSC32_IN: C12.1, IC5.8 (P14), Q2.1
OSC32_OUT: C13.1, IC5.9 (P15), Q2.2
PHY_RESET: IC5.30 (P6); also elsewhere on the board
SPI2_MISO: IC5.53 (P14), IC6.33 (TP_DOUT)
SPI2_MOSI: IC5.54 (P15), IC6.31 (TP_DIN)
SPI2_SCK: IC5.71 (P12), IC6.29 (TP_CLK)
SPI3_MISO: IC5.79 (P11); also elsewhere on the board
SPI3_MOSI: IC5.80 (P12); also elsewhere on the board
SPI3_SCK: IC5.78 (P10); also elsewhere on the board
SRST: C14.1, IC5.14 (~RST), RESET1.3, RESET1.4; also elsewhere on the board
SWCLK: IC5.76 (P14); also elsewhere on the board
SWDIO: IC5.72 (P13); also elsewhere on the board
TP_CS: IC5.63 (P6), IC6.30 (TP_CS)
TP_IRQ: IC5.59 (P12), IC6.34 (TP_IRQ)
USART1_RX: IC5.93 (P7); also elsewhere on the board
USART1_TX: IC5.92 (P6); also elsewhere on the board
VBAT: IC5.6 (VBAT), X1.POS1, X1.POS2
WF1_BUSY: IC5.83 (P2); also elsewhere on the board
WF1_CS: IC5.87 (P6); also elsewhere on the board
WF1_IRQ: IC5.84 (P3); also elsewhere on the board
WF_ANT: IC5.5 (P6); also elsewhere on the board
WF_CPS: IC5.1 (P2); also elsewhere on the board
WF_CRX: IC5.3 (P4); also elsewhere on the board
WF_CTX: IC5.2 (P3); also elsewhere on the board
WF_ON: IC5.91 (P5); also elsewhere on the board

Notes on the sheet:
130mA
LCD
Main Processor
Design: A. Ryll
Do not use PB4~~{}

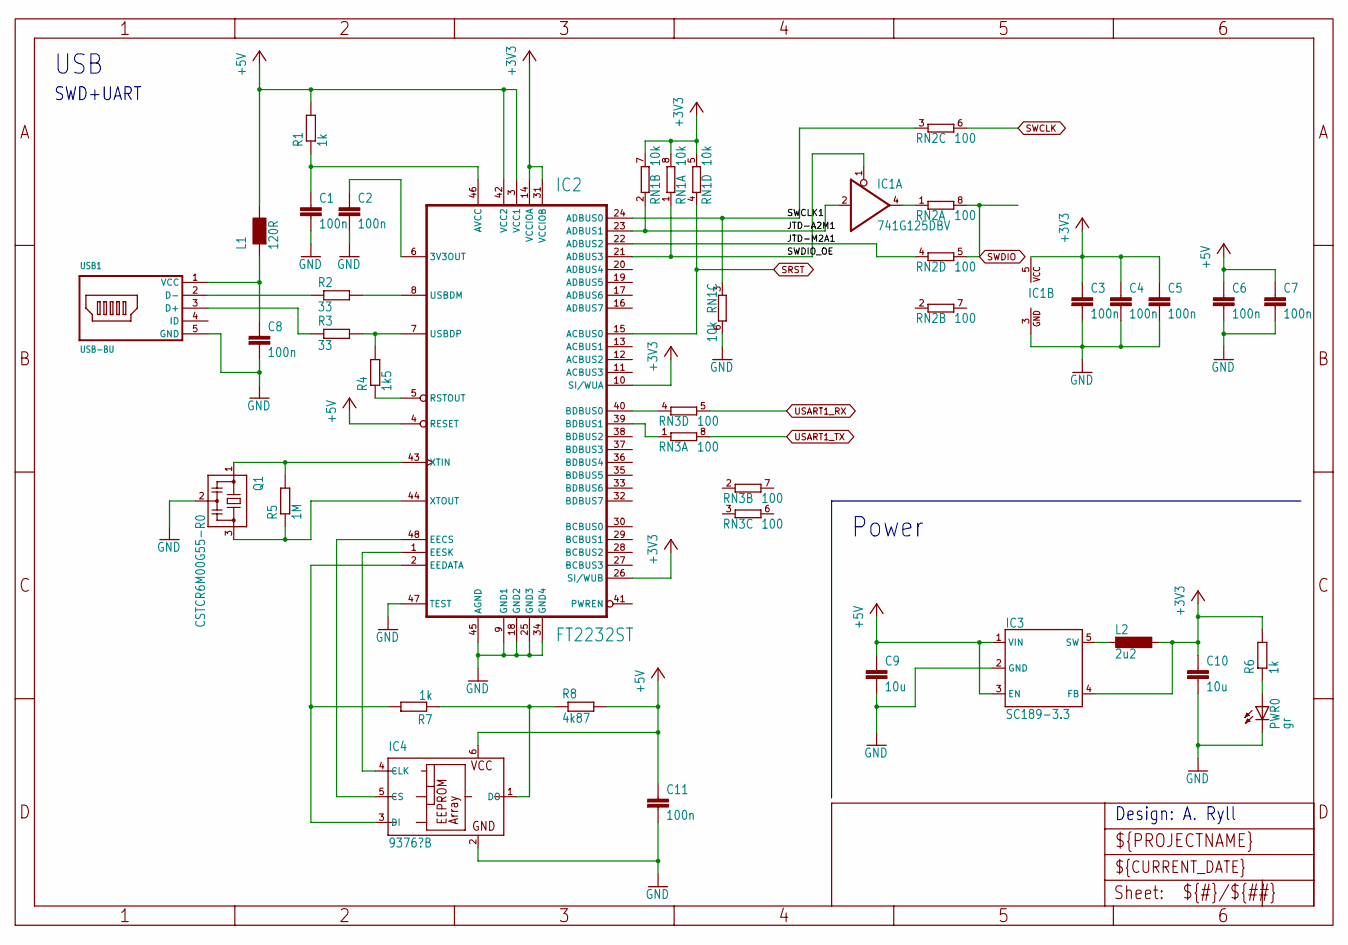
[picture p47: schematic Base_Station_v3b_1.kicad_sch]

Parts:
C1, C2, C3, C4, C5, C6, C7, C8, C11: 100n; C0603
C9, C10: 10u; C0603
IC1: 741G125DBV; SOT23-5
IC2: FT2232ST; LQFP48-ST
IC3: SC189-3.3; SOT23-5
IC4: 9376?B; SOT23-6
L1: 120R; 0603
L2: 2u2; IHLP1616
PWR0: gr; CHIP-LED0603
Q1: CSTCR6M00G55-R0; CSTCR6M
R1, R6, R7: 1k; R0603
R2, R3: 33; R0603
R4: 1k5; R0603
R5: 1M; R0603
R8: 4k87; R0603
RN1: 10k; EXB28V
RN2, RN3: 100; EXB28V
USB1: USB-BU; USB-BMICRO

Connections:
+3V3: C3.1, C4.1, C5.1, C10.1, IC1.5 (VCC), IC2.10 (SI/WUA), IC2.14 (VCCIOA), IC2.26 (SI/WUB), IC2.31 (VCCIOB), IC3.4 (FB), L2.P$1 (1), R6.2, RN1.5 (2), RN1.7 (2), RN1.8 (2); also elsewhere on the board
+5V: C6.1, C7.1, C9.1, C11.1, IC2.3 (VCC1), IC2.4 (RESET), IC2.42 (VCC2), IC3.1 (VIN), IC3.3 (EN), IC4.6 (VCC), L1.2, R1.2, R8.2; also elsewhere on the board
GND: C1.2, C2.2, C3.2, C4.2, C5.2, C6.2, C7.2, C8.2, C9.2, C10.2, C11.2, IC1.3 (GND), IC2.9 (GND1), IC2.18 (GND2), IC2.25 (GND3), IC2.34 (GND4), IC2.45 (AGND), IC2.47 (TEST), IC3.2 (GND), IC4.2 (GND), PWR0.C, Q1.2, RN1.6 (2), USB1.5 (GND); also elsewhere on the board
JTD-A2M1: IC1.2 (I), IC2.23 (ADBUS1), RN1.2 (1)
JTD-M2A1: IC2.22 (ADBUS2), RN2.4 (1)
unnamed: IC2.48 (EECS), IC4.5 (CS)
unnamed: IC2.1 (EESK), IC4.4 (CLK)
unnamed: IC2.2 (EEDATA), IC4.3 (DI), R7.2
unnamed: IC2.44 (XTOUT), Q1.3, R5.1
unnamed: IC4.1 (DO), R7.1, R8.1
unnamed: PWR0.A, R6.1
unnamed: IC1.4 (O), RN2.1
unnamed: IC2.40 (BDBUS0), RN3.4 (1)
unnamed: IC2.39 (BDBUS1), RN3.1
unnamed: IC2.7 (USBDP), R3.2, R4.2
unnamed: IC2.8 (USBDM), R2.2
unnamed: IC2.5 (RSTOUT), R4.1
unnamed: C2.1, IC2.6 (3V3OUT)
unnamed: C8.1, L1.1, USB1.1 (VCC)
unnamed: R2.1, USB1.2 (D-)
unnamed: R3.1, USB1.3 (D+)
unnamed: C1.1, IC2.46 (AVCC), R1.1
unnamed: IC2.43 (XTIN), Q1.1, R5.2
SRST: IC2.15 (ACBUS0), RN1.4 (1); also elsewhere on the board
SW-OUT: IC3.5 (SW), L2.P$2 (2)
SWCLK: RN2.6 (2); also elsewhere on the board
SWCLK1: IC2.24 (ADBUS0), RN1.3 (1), RN2.3 (1)
SWDIO: RN2.5 (2), RN2.8 (2); also elsewhere on the board
SWDIO_OE: IC1.1 (OE), IC2.21 (ADBUS3), RN1.1
USART1_RX: RN3.5 (2); also elsewhere on the board
USART1_TX: RN3.8 (2); also elsewhere on the board

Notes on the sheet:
Design: A. Ryll
USB
Power
SWD+UART

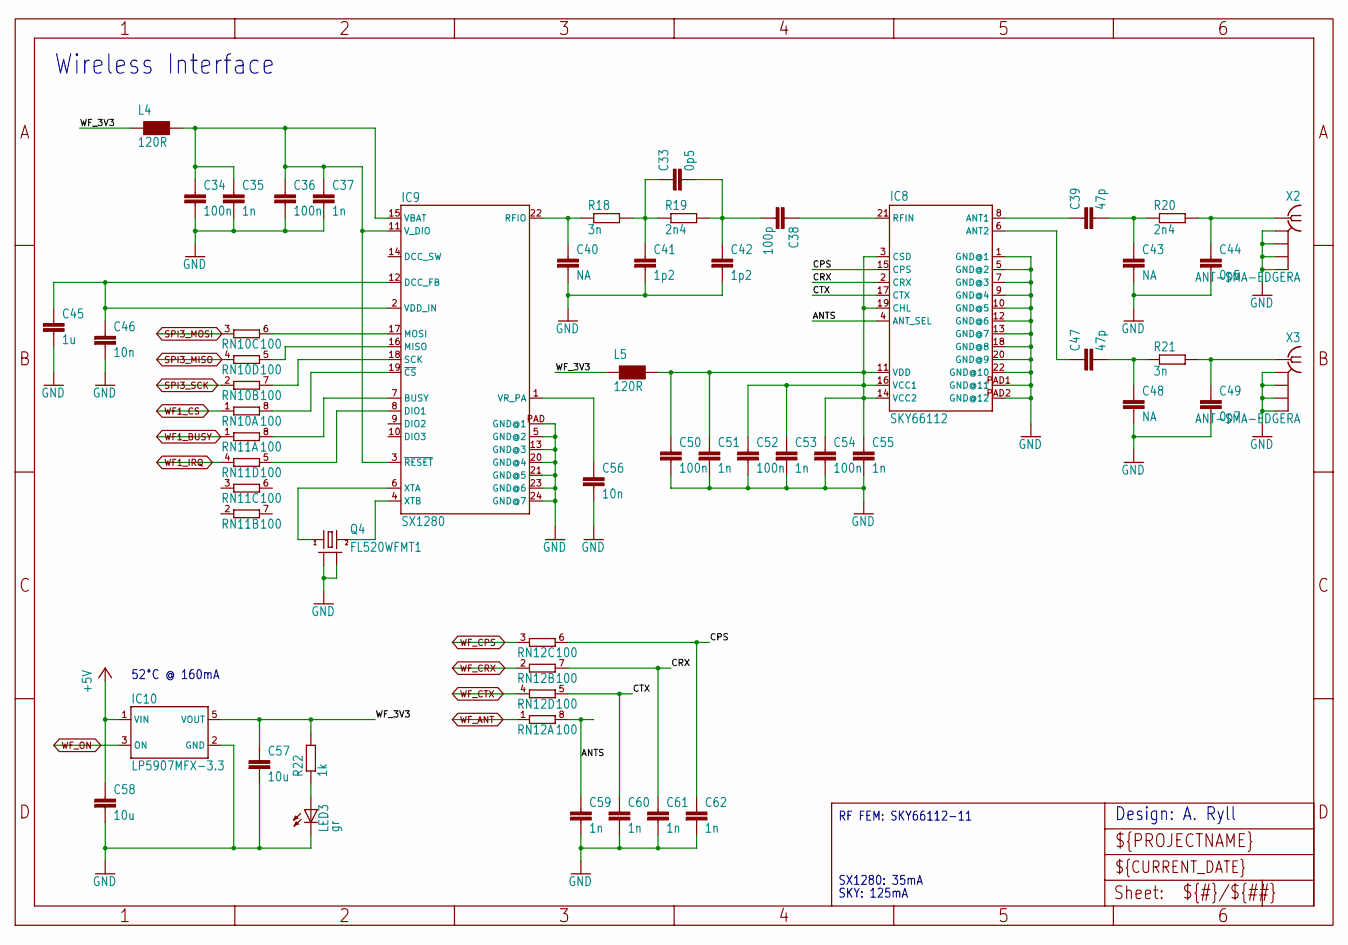
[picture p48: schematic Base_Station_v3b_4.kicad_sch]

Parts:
C33, C44: 0p5; C0402
C34, C36, C50, C52, C54: 100n; C0603
C35, C37, C51, C53, C55, C59, C60, C61, C62: 1n; C0603
C38: 100p; C0402
C39, C47: 47p; C0402
C40, C43, C48: NA; C0402
C41, C42: 1p2; C0402
C45: 1u; C0603
C46, C56: 10n; C0603
C49: 0p7; C0402
C57, C58: 10u; C0603
IC8: SKY66112; SMCM-22
IC9: SX1280; QFN24L
IC10: LP5907MFX-3.3; SOT23-5L
L4, L5: 120R; 0603
LED3: gr; CHIP-LED0603
Q4: FL520WFMT1; CRYSTAL-7M
R18, R21: 3n; R0402
R19, R20: 2n4; R0402
R22: 1k; R0603
RN10, RN11, RN12: 100; EXB28V
X2, X3: ANT-SMA-EDGERA; ANT-SMA-RA

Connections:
+5V: C58.1, IC10.1 (VIN); also elsewhere on the board
ANTS: C59.1, IC8.4 (ANT_SEL), RN12.8 (2)
CPS: C62.1, IC8.15 (CPS), RN12.6 (2)
CRX: C61.1, IC8.2 (CRX), RN12.7 (2)
CTX: C60.1, IC8.17 (CTX), RN12.5 (2)
GND: C34.2, C35.2, C36.2, C37.2, C40.2, C41.2, C42.2, C43.2, C44.2, C45.2, C46.2, C48.2, C49.2, C50.2, C51.2, C52.2, C53.2, C54.2, C55.2, C56.2, C57.2, C58.2, C59.2, C60.2, C61.2, C62.2, IC8.1 (GND@1), IC8.5 (GND@2), IC8.7 (GND@3), IC8.9 (GND@4), IC8.10 (GND@5), IC8.12 (GND@6), IC8.13 (GND@7), IC8.18 (GND@8), IC8.20 (GND@9), IC8.22 (GND@10), IC8.PAD1 (GND@11), IC8.PAD2 (GND@12), IC9.5 (GND@2), IC9.13 (GND@3), IC9.20 (GND@4), IC9.21 (GND@5), IC9.23 (GND@6), IC9.24 (GND@7), IC9.PAD (GND@1), IC10.2 (GND), LED3.C, Q4.2 (GND1), Q4.4 (GND2), X2.GND1 (GND), X2.GND2 (GND1), X2.GND3 (GND2), X2.GND4 (GND3), X3.GND1 (GND), X3.GND2 (GND1), X3.GND3 (GND2), X3.GND4 (GND3); also elsewhere on the board
unnamed: IC9.17 (MOSI), RN10.6 (2)
unnamed: IC9.16 (MISO), RN10.5 (2)
unnamed: IC9.18 (SCK), RN10.7 (2)
unnamed: IC9.19 (~CS), RN10.8 (2)
unnamed: IC9.7 (BUSY), RN11.8 (2)
unnamed: IC9.8 (DIO1), RN11.5 (2)
unnamed: LED3.A, R22.1
unnamed: IC9.6 (XTA), Q4.1
unnamed: IC9.4 (XTB), Q4.3 (2)
unnamed: C33.1, C41.1, R18.2, R19.1
unnamed: C33.2, C38.2, C42.1, R19.2
unnamed: C56.1, IC9.1 (VR_PA)
unnamed: C45.1, C46.1, IC9.2 (VDD_IN), IC9.12 (DCC_FB)
unnamed: C38.1, IC8.21 (RFIN)
unnamed: C39.2, C43.1, R20.1
unnamed: C44.1, R20.2, X2.C (1)
unnamed: C47.2, C48.1, R21.1
unnamed: C49.1, R21.2, X3.C (1)
unnamed: C39.1, IC8.8 (ANT1)
unnamed: C47.1, IC8.6 (ANT2)
RFIO1: C40.1, IC9.22 (RFIO), R18.1
SPI3_MISO: RN10.4 (1); also elsewhere on the board
SPI3_MOSI: RN10.3 (1); also elsewhere on the board
SPI3_SCK: RN10.2 (1); also elsewhere on the board
WF1_BUSY: RN11.1; also elsewhere on the board
WF1_CS: RN10.1; also elsewhere on the board
WF1_IRQ: RN11.4 (1); also elsewhere on the board
WF_3V3: C57.1, IC10.5 (VOUT), L4.1, L5.1, R22.2
WF_3V3FEM: C50.1, C51.1, C52.1, C53.1, C54.1, C55.1, IC8.3 (CSD), IC8.11 (VDD), IC8.14 (VCC2), IC8.16 (VCC1), IC8.19 (CHL), L5.2
WF_3V3SX: C34.1, C35.1, C36.1, C37.1, IC9.3 (~RESET), IC9.11 (V_DIO), IC9.15 (VBAT), L4.2
WF_ANT: RN12.1; also elsewhere on the board
WF_CPS: RN12.3 (1); also elsewhere on the board
WF_CRX: RN12.2 (1); also elsewhere on the board
WF_CTX: RN12.4 (1); also elsewhere on the board
WF_ON: IC10.3 (ON); also elsewhere on the board

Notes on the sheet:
SX1280: 35mA
52°C @ 160mA
Wireless Interface
RF FEM: SKY66112-11
SKY: 125mA
Design: A. Ryll

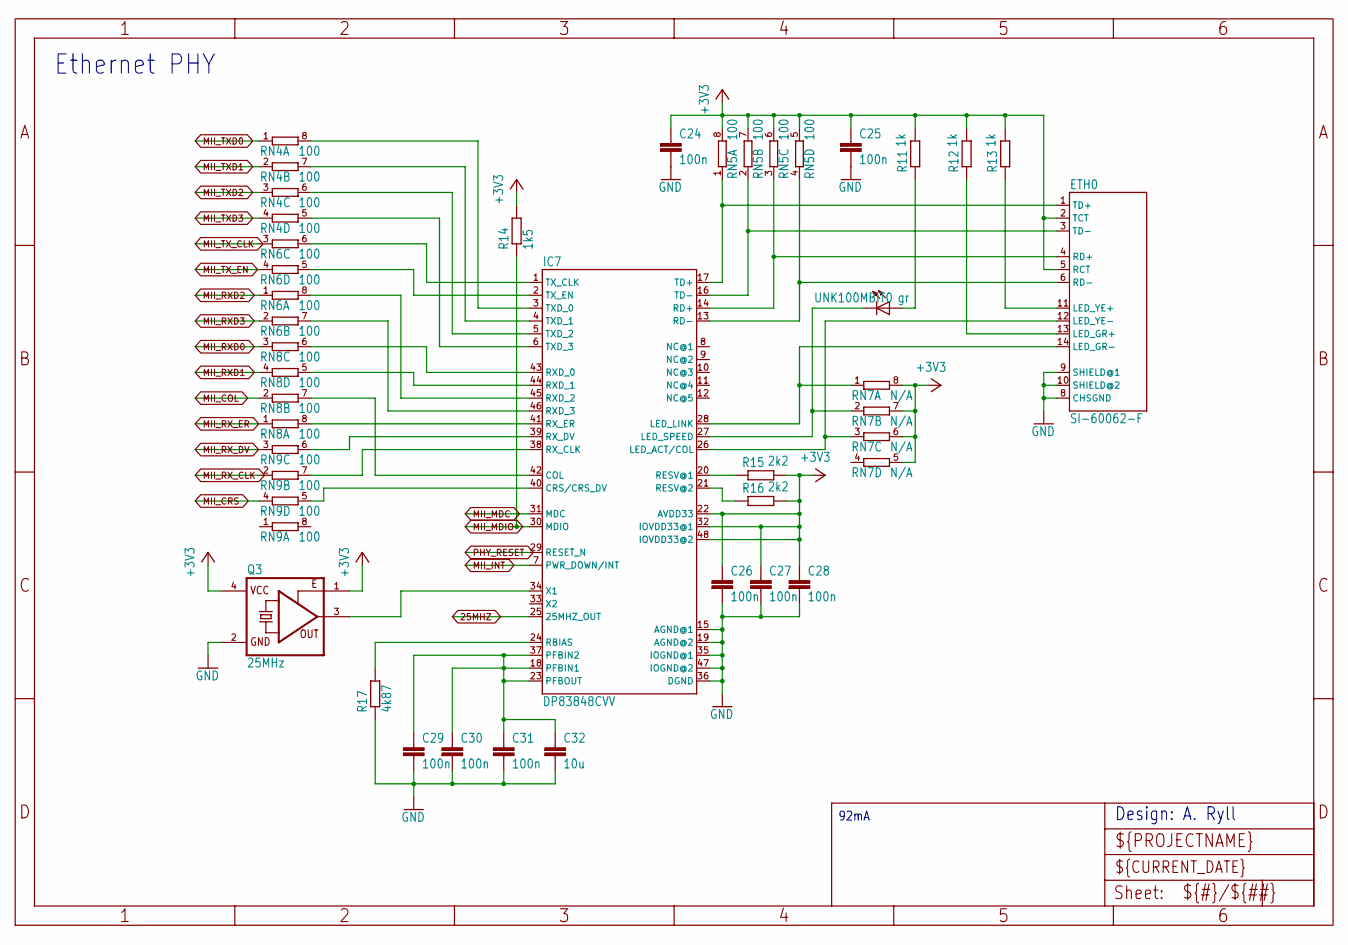
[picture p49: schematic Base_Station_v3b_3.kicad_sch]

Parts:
C24, C25, C26, C27, C28, C29, C30, C31: 100n; C0603
C32: 10u; C0603
ETH0: SI-60062-F; RJ45-LED
IC7: DP83848CVV; LQFP48
Q3: 25MHz; 7X
R11, R12, R13: 1k; R0603
R14: 1k5; R0603
R15, R16: 2k2; R0603
R17: 4k87; R0603
RN4, RN5, RN6, RN8, RN9: 100; EXB28V
RN7: N/A; EXB28V
UNK100MBIT0: gr; CHIP-LED0603

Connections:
25MHZ: IC7.25 (25MHZ_OUT); also elsewhere on the board
+3V3: C24.1, C25.1, C26.1, C27.1, C28.1, ETH0.2 (TCT), ETH0.5 (RCT), IC7.22 (AVDD33), IC7.32 (IOVDD33@1), IC7.48 (IOVDD33@2), Q3.1 (OE), Q3.4 (VCC), R11.2, R12.2, R13.2, R14.2, R15.2, R16.2, RN5.5 (2), RN5.6 (2), RN5.7 (2), RN5.8 (2), RN7.5 (2), RN7.6 (2), RN7.7 (2), RN7.8 (2); also elsewhere on the board
GND: C24.2, C25.2, C26.2, C27.2, C28.2, C29.2, C30.2, C31.2, C32.2, ETH0.8 (CHSGND), ETH0.9 (SHIELD@1), ETH0.10 (SHIELD@2), IC7.15 (AGND@1), IC7.19 (AGND@2), IC7.35 (IOGND@1), IC7.36 (DGND), IC7.47 (IOGND@2), Q3.2 (GND), R17.1; also elsewhere on the board
MII_COL: RN8.2 (1); also elsewhere on the board
MII_CRS: RN9.4 (1); also elsewhere on the board
MII_INT: IC7.7 (PWR_DOWN/INT); also elsewhere on the board
MII_MDC: IC7.31 (MDC); also elsewhere on the board
MII_MDIO: IC7.30 (MDIO), R14.1; also elsewhere on the board
MII_RXD0: RN8.3 (1); also elsewhere on the board
MII_RXD1: RN8.4 (1); also elsewhere on the board
MII_RXD2: RN6.1; also elsewhere on the board
MII_RXD3: RN6.2 (1); also elsewhere on the board
MII_RX_CLK: RN9.2 (1); also elsewhere on the board
MII_RX_DV: RN9.3 (1); also elsewhere on the board
MII_RX_ER: RN8.1; also elsewhere on the board
MII_TXD0: RN4.1; also elsewhere on the board
MII_TXD1: RN4.2 (1); also elsewhere on the board
MII_TXD2: RN4.3 (1); also elsewhere on the board
MII_TXD3: RN4.4 (1); also elsewhere on the board
MII_TX_CLK: RN6.3 (1); also elsewhere on the board
MII_TX_EN: RN6.4 (1); also elsewhere on the board
unnamed: IC7.3 (TXD_0), RN4.8 (2)
unnamed: IC7.4 (TXD_1), RN4.7 (2)
unnamed: IC7.5 (TXD_2), RN4.6 (2)
unnamed: IC7.6 (TXD_3), RN4.5 (2)
unnamed: IC7.1 (TX_CLK), RN6.6 (2)
unnamed: IC7.2 (TX_EN), RN6.5 (2)
unnamed: IC7.45 (RXD_2), RN6.8 (2)
unnamed: IC7.46 (RXD_3), RN6.7 (2)
unnamed: IC7.43 (RXD_0), RN8.6 (2)
unnamed: IC7.44 (RXD_1), RN8.5 (2)
unnamed: IC7.42 (COL), RN8.7 (2)
unnamed: IC7.41 (RX_ER), RN8.8 (2)
unnamed: IC7.39 (RX_DV), RN9.6 (2)
unnamed: IC7.38 (RX_CLK), RN9.7 (2)
unnamed: IC7.40 (CRS/CRS_DV), RN9.5 (2)
unnamed: IC7.24 (RBIAS), R17.2
unnamed: C29.1, C30.1, C31.1, C32.1, IC7.18 (PFBIN1), IC7.23 (PFBOUT), IC7.37 (PFBIN2)
unnamed: IC7.20 (RESV@1), R15.1
unnamed: IC7.21 (RESV@2), R16.1
unnamed: ETH0.12 (LED_YE-), IC7.26 (LED_ACT/COL), RN7.3 (1)
unnamed: IC7.27 (LED_SPEED), RN7.2 (1), UNK100MBIT0.C
unnamed: ETH0.14 (LED_GR-), IC7.28 (LED_LINK), RN7.1
unnamed: ETH0.6 (RD-), IC7.13 (RD-), RN5.4 (1)
unnamed: ETH0.4 (RD+), IC7.14 (RD+), RN5.3 (1)
unnamed: ETH0.3 (TD-), IC7.16 (TD-), RN5.2 (1)
unnamed: ETH0.1 (TD+), IC7.17 (TD+), RN5.1
unnamed: R11.1, UNK100MBIT0.A
unnamed: ETH0.13 (LED_GR+), R12.1
unnamed: ETH0.11 (LED_YE+), R13.1
unnamed: IC7.34 (X1), Q3.3 (FO)
PHY_RESET: IC7.29 (RESET_N); also elsewhere on the board

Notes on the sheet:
Ethernet PHY
92mA
Design: A. Ryll

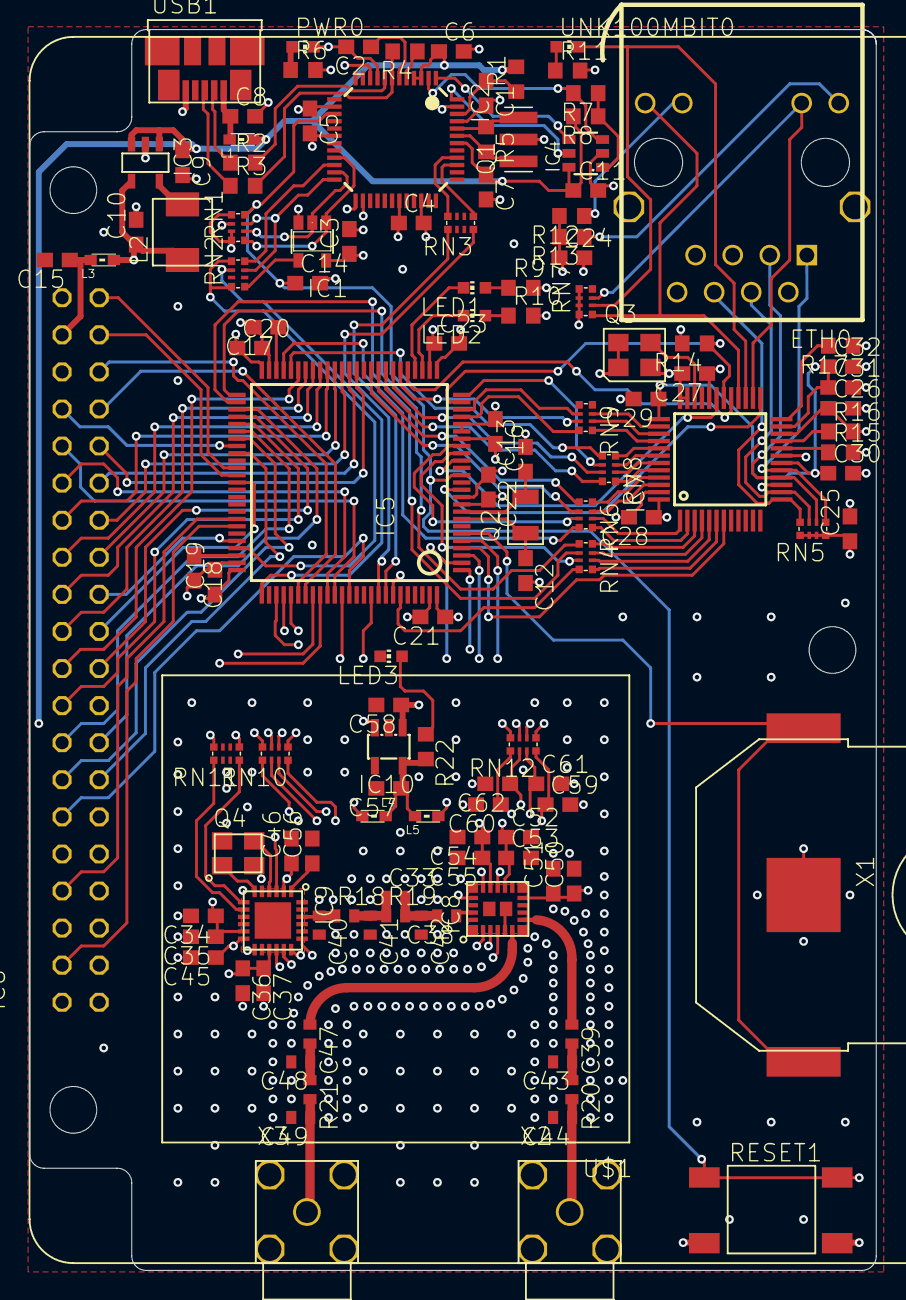
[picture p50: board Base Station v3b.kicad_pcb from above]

Board: 4 copper layers, 58.0 x 85.0 mm, 130 parts (0 on the bottom side), 157 nets.

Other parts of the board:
@HOLE0, @HOLE1, @HOLE2: (no value)
U$1: BMI-S-204-F; SHIELD-32MM

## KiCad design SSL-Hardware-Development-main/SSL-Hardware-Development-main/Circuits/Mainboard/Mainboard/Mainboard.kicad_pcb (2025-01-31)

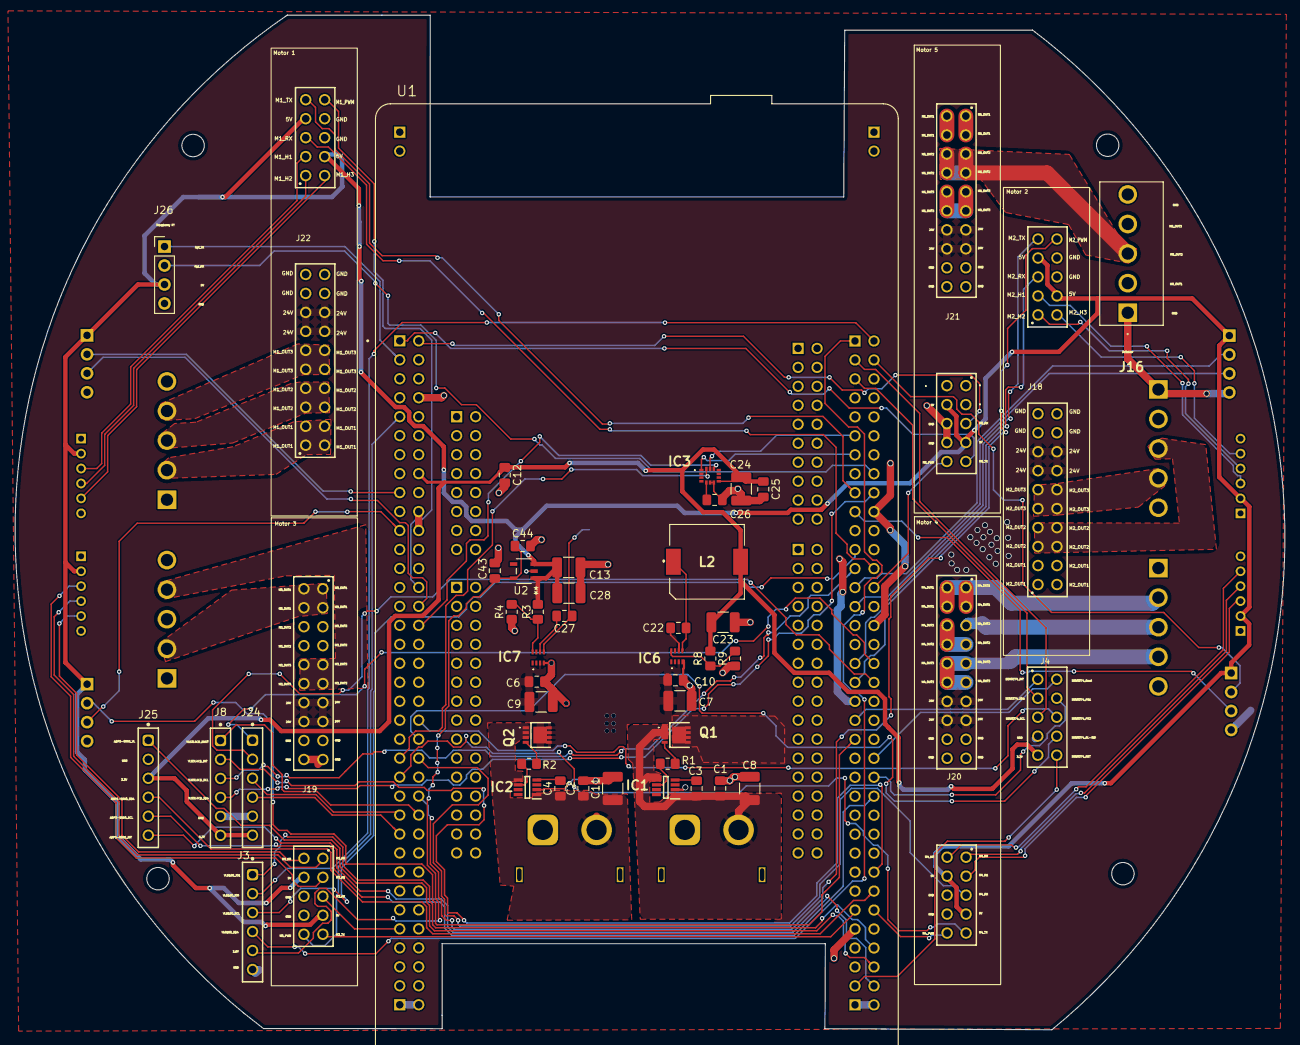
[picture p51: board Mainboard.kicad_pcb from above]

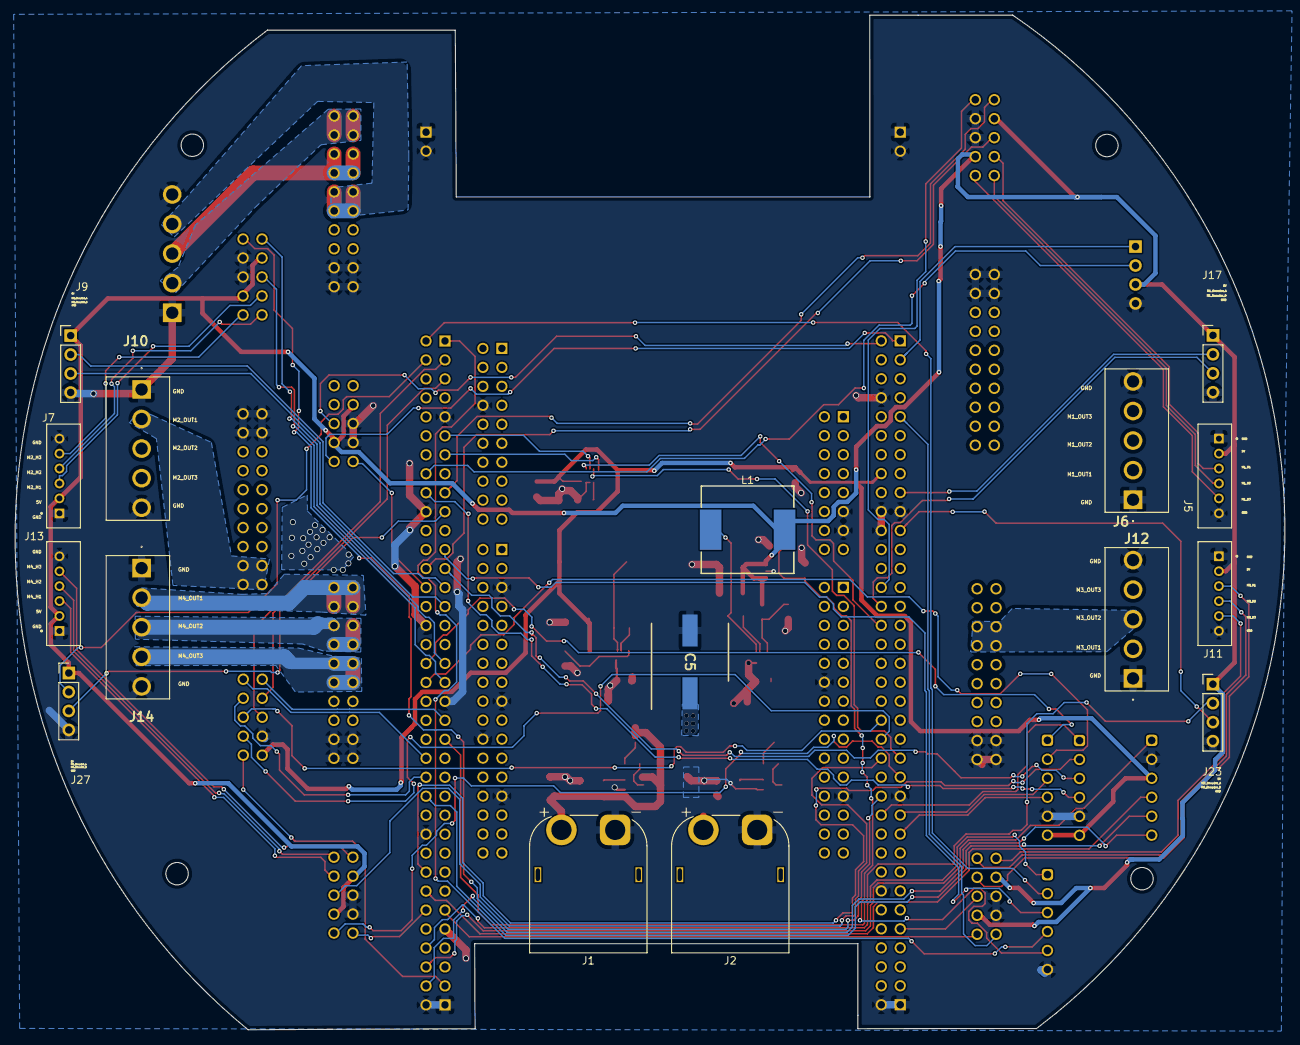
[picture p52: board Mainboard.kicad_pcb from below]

Board: 2 copper layers, 170.0 x 135.9 mm, 65 parts (16 on the bottom side), 100 nets.

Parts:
C1, C2, C3, C4, C6, C10, C12, C22, C25, C26, C27, C44: 0.1uF; C_0805_2012Metric_Pad1.18x1.45mm_HandSolder
C5: 220uF; CAPAE1030X1050N
C7, C8, C9, C11, C13, C24: 10uF; C_1210_3225Metric_Pad1.33x2.70mm_HandSolder
C23, C28: 47uF; C_1210_3225Metric_Pad1.33x2.70mm_HandSolder
C43: 4.7uF; C_0805_2012Metric_Pad1.18x1.45mm_HandSolder
IC1, IC2: LM74500QDDFRQ1; SOT65P280X110-8N
IC3: 2536030320001
IC6, IC7: TPS563300DRLR; TPS62932DRLR
J1, J2: XT60PW-M; AMASS_XT60PW-M_1x02_P7.20mm_Horizontal
J3, J8, J24, J25: Conn_01x06_Pin; 61300611821
J4: 61301021821
J5, J7, J11, J13: B6B-PH-K-S; JST_B6B-PH-K-S
J6, J10, J12, J14, J16: B5P-VH_LF__SN_
J9, J17, J23, J26, J27: Conn_01x04_Pin; PinHeader_1x04_P2.54mm_Vertical
J18, J19, J20, J21, J22: ESC_Adapter_socket
L1: 8.2uH; WE-HCC_1210
L2: 5.6uH; 7447714220
Q1, Q2: PSMN6R7-40MLDX; PSMN6R740MLDX
R1, R2: 10; R_0805_2012Metric_Pad1.20x1.40mm_HandSolder
R3: 52.3kOhm; R_0805_2012Metric_Pad1.20x1.40mm_HandSolder
R4, R9: 10kOhm; R_0805_2012Metric_Pad1.20x1.40mm_HandSolder
R8: 30.9kOhm; R_0805_2012Metric_Pad1.20x1.40mm_HandSolder
U1: NUCLEOH723ZG; MODULE_NUCLEOH723ZG
U2: ADP121-AUJZ28R7; UJ-5_ADI

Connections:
2.8V: C43.1, C44.1, J3.5, U2.5 (VOUT)
3.3V: C12.1, C23.2, C24.1, C25.1, IC3.8 (VDD), J4.9, J8.6, J24.6, J25.3, L2.2, R8.2, U1.CN11_16 (3V3)
5V: C13.1, C28.1, J5.2, J7.2, J9.1, J11.2, J13.2, J17.1, J18.24, J18.27, J19.24, J19.27, J20.24, J20.27, J21.24, J21.27, J22.24, J22.27, J23.1, J26.3, J27.1, L1.2, R3.2, U2.1 (VIN), U2.3 (EN)
24V: C5.1, C6.1, C7.1, C9.1, C10.1, IC6.3 (VIN), IC7.3 (VIN), J18.13, J18.14, J18.15, J18.16, J19.13, J19.14, J19.15, J19.16, J20.13, J20.14, J20.15, J20.16, J21.13, J21.14, J21.15, J21.16, J22.13, J22.14, J22.15, J22.16, Q1.5 (D_1), Q1.6 (D_2), Q1.7 (D_3), Q1.8 (D_4), Q1.9 (D_5), Q1.10 (D_6), Q1.11 (D_7), Q2.5 (D_1), Q2.6 (D_2), Q2.7 (D_3), Q2.8 (D_4), Q2.9 (D_5), Q2.10 (D_6), Q2.11 (D_7)
/24V_1: C1.1, C3.1, C8.1, IC1.1 (EN), IC1.5 (SOURCE), J1.2, Q1.1 (S_1), Q1.2 (S_2), Q1.3 (S_3)
/24V_2: C2.1, C4.1, C11.1, IC2.1 (EN), IC2.5 (SOURCE), J2.2, Q2.1 (S_1), Q2.2 (S_2), Q2.3 (S_3)
/ADPS-9960_INT: J25.6, U1.CN12_70 (PG6)
/ADPS-9960_SCL: J25.5, U1.CN12_50 (PF14)
/ADPS-9960_SDA: J25.4, U1.CN12_60 (PF15)
/ADPS-9960_VL: J25.1, U1.CN12_68 (PG5)
/M1_Encoder_A: J17.2, U1.CN11_17 (PA15)
/M1_Encoder_B: J17.3, U1.CN11_30 (PA1)
/M1_H1: J5.3, J22.23
/M1_H2: J5.4, J22.21
/M1_H3: J5.5, J22.22
/M1_OUT1: J6.2, J22.1, J22.2, J22.3, J22.4
/M1_OUT2: J6.3, J22.5, J22.6, J22.7, J22.8
/M1_OUT3: J6.4, J22.9, J22.10, J22.11, J22.12
/M1_PWM: J22.30, U1.CN11_28 (PA0)
/M1_RX: J22.25, U1.CN12_26 (PB15)
/M1_TX: J22.29, U1.CN12_17 (PB6)
/M2_Encoder_A: J9.2, U1.CN12_27 (PB4)
/M2_Encoder_B: J9.3, U1.CN12_29 (PB5)
/M2_H1: J7.3, J18.23
/M2_H2: J7.4, J18.21
/M2_H3: J7.5, J18.22
/M2_OUT1: J10.2, J18.1, J18.2, J18.3, J18.4
/M2_OUT2: J10.3, J18.5, J18.6, J18.7, J18.8
/M2_OUT3: J10.4, J18.9, J18.10, J18.11, J18.12
/M2_PWM: J18.30, U1.CN11_50 (PE5)
/M2_RX: J18.25, U1.CN12_37 (PA3)
/M2_TX: J18.29, U1.CN12_35 (PA2)
/M3_Encoder_A: J23.2, U1.CN12_43 (PD12)
/M3_Encoder_B: J23.3, U1.CN11_21 (PB7)
/M3_H1: J11.3, J19.23
/M3_H2: J11.4, J19.21
/M3_H3: J11.5, J19.22
/M3_OUT1: J12.2, J19.1, J19.2, J19.3, J19.4
/M3_OUT2: J12.3, J19.5, J19.6, J19.7, J19.8
/M3_OUT3: J12.4, J19.9, J19.10, J19.11, J19.12
/M3_PWM: J19.30, U1.CN11_9 (PF6)
/M3_RX: J19.25, U1.CN11_63 (PG9)
/M3_TX: J19.29, U1.CN12_61 (PG14)
/M4_Encoder_A: J27.2, U1.CN12_4 (PC6)
/M4_Encoder_B: J27.3, U1.CN12_19 (PC7)
/M4_H1: J13.3, J20.23
/M4_H2: J13.4, J20.21
/M4_H3: J13.5, J20.22
/M4_OUT1: J14.2, J20.1, J20.2, J20.3, J20.4
/M4_OUT2: J14.3, J20.5, J20.6, J20.7, J20.8
/M4_OUT3: J14.4, J20.9, J20.10, J20.11, J20.12
/M4_PWM: J20.30, U1.CN12_62 (PF11)
/M4_RX: J20.25, U1.CN11_46 (PE2)
/M4_TX: J20.29, U1.CN11_47 (PE3)
/M5_OUT1: J16.2, J21.1, J21.2, J21.3, J21.4
/M5_OUT2: J16.3, J21.5, J21.6, J21.7, J21.8
/M5_OUT3: J16.4, J21.9, J21.10, J21.11, J21.12
/M5_PWM: J21.30, U1.CN12_28 (PB14)
/M5_RX: J21.25, U1.CN11_2 (PC11)
/M5_TX: J21.29, U1.CN11_1 (PC10)
/Rpi_RX: J26.2, U1.CN12_16 (PB12)
/Rpi_TX: J26.1, U1.CN11_3 (PC12)
/SEN0374_BL-IND: J4.8, U1.CN11_44 (PG3)
/SEN0374_Boot: J4.2, U1.CN12_46 (PD14)
/SEN0374_INT: J4.1, U1.CN12_41 (PD13)
/SEN0374_PS1: J4.4, U1.CN12_48 (PD15)
/SEN0374_PS2: J4.6, U1.CN11_42 (PG2)
/SEN0374_RST: J4.10, U1.CN12_69 (PG4)
/SEN0374_SCL: J4.5, U1.CN12_3 (PB8)
/SEN0374_SDA: J4.3, U1.CN12_5 (PB9)
/VL53L4CD2_INT: J24.2, U1.CN12_38 (PF4)
/VL53L4CD2_SCL: J24.3, U1.CN11_51 (PF1)
/VL53L4CD2_SDA: J24.4, U1.CN11_53 (PF0)
/VL53L4CD2_SHUT: J24.1, U1.CN12_36 (PF5)
/VL53L4CD_INT: J8.2, U1.CN12_58 (PF3)
/VL53L4CD_SCL: J8.3, U1.CN12_25 (PB10)
/VL53L4CD_SDA: J8.4, U1.CN12_18 (PB11)
/VL53L4CD_SHUT: J8.1, U1.CN11_52 (PF2)
/VL6180_IO0: J3.2, U1.CN12_2 (PC8)
/VL6180_IO1: J3.1, U1.CN12_66 (PG8)
/VL6180_SCL: J3.3, U1.CN12_23 (PA8)
/VL6180_SDA: J3.4, U1.CN12_1 (PC9)
GND: C1.2, C2.2, C5.2, C6.2, C7.2, C8.2, C9.2, C10.2, C11.2, C12.2, C13.2, C23.1, C24.2, C25.2, C26.2, C28.2, C43.2, C44.2, IC1.2 (GND), IC2.2 (GND), IC3.6 (GND_1), IC3.7 (GND_2), IC6.4 (GND), IC7.4 (GND), J1.1, J2.1, J3.6, J4.7, J5.1, J5.6, J6.1, J6.5, J7.1, J7.6, J8.5, J9.4, J10.1, J10.5, J11.1, J11.6, J12.1, J12.5, J13.1, J13.6, J14.1, J14.5, J16.1, J16.5, J17.4, J18.17, J18.18, J18.19, J18.20, J18.26, J18.28, J19.17, J19.18, J19.19, J19.20, J19.26, J19.28, J20.17, J20.18, J20.19, J20.20, J20.26, J20.28, J21.17, J21.18, J21.19, J21.20, J21.26, J21.28, J22.17, J22.18, J22.19, J22.20, J22.26, J22.28, J23.4, J24.5, J25.2, J26.4, J27.4, R4.1, R9.1, U1.CN3_1 (GND_CN3), U1.CN3_2 (GND_CN3), U1.CN4_1 (GND_CN4), U1.CN4_2 (GND_CN4), U1.CN7_8 (GND_CN7), U1.CN8_11 (GND_CN8), U1.CN8_13 (GND_CN8), U1.CN9_12 (GND_CN9), U1.CN9_23 (GND_CN9), U1.CN10_5 (GND_CN10), U1.CN10_17 (GND_CN10), U1.CN10_22 (GND_CN10), U1.CN10_27 (GND_CN10), U1.CN11_8 (GND_CN11), U1.CN11_19 (GND_CN11), U1.CN11_20 (GND_CN11), U1.CN11_22 (GND_CN11), U1.CN11_49 (GND_CN11), U1.CN11_60 (GND_CN11), U1.CN12_9 (GND_CN12), U1.CN12_20 (GND_CN12), U1.CN12_32 (AGND_CN12), U1.CN12_39 (GND_CN12), U1.CN12_54 (GND_CN12), U1.CN12_63 (GND_CN12), U1.CN15_1 (GND_CN15), U1.CN15_2 (GND_CN15), U1.CN16_1 (GND_CN16), U1.CN16_2 (GND_CN16), U2.2 (GND)
unnamed: IC1.6 (GATE), R1.2
unnamed: C3.2, IC1.4 (VCAP)
unnamed: IC2.6 (GATE), R2.2
unnamed: C4.2, IC2.4 (VCAP)
unnamed: C22.2, IC6.6 (BST)
unnamed: IC6.8 (FB), R8.1, R9.2
unnamed: C22.1, IC6.5 (SW), L2.1
unnamed: C27.2, IC7.6 (BST)
unnamed: IC7.8 (FB), R3.1, R4.2
unnamed: C27.1, IC7.5 (SW), L1.1
unnamed: Q1.4 (G), R1.1
unnamed: Q2.4 (G), R2.1
VDD_IO: C26.1, IC3.5 (VDD_IO)
WSENS_CS: IC3.12 (CS), U1.CN11_32 (PA4)
WSENS_SAO: IC3.1 (SAO), U1.CN12_13 (PA6)
WSENS_SCL: IC3.13 (SCL), U1.CN12_11 (PA5)
WSENS_SDA: IC3.14 (SDA), U1.CN11_45 (PD7)

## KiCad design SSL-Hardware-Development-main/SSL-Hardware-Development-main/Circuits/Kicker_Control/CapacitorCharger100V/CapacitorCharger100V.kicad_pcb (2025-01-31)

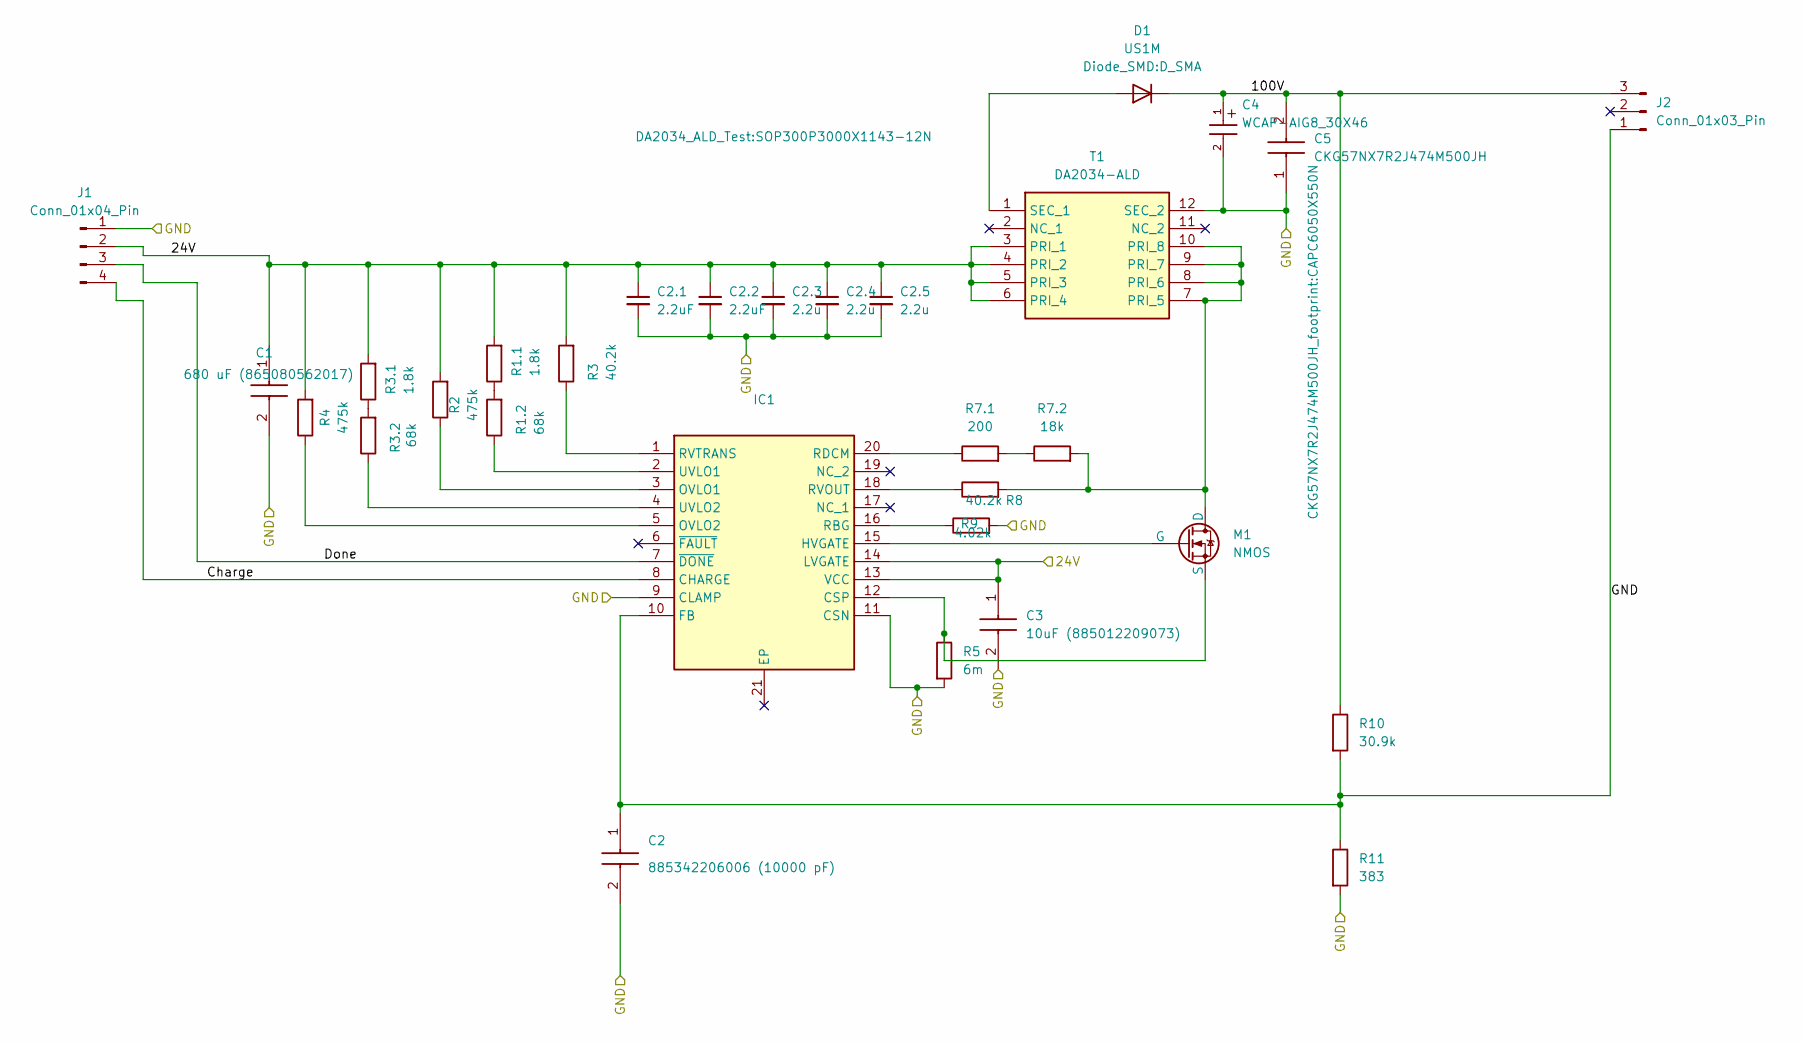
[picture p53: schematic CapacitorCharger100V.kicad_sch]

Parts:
C1: 680 uF (865080562017); CAPAE1350X1400N; Mouser Part Number 710-865080562017
C2: 885342206006 (10000 pF); CAPC1608X87N; Mouser Part Number 710-885342206006
C2.1, C2.2: 2.2uF; C_1210_3225Metric
C2.3, C2.4, C2.5: 2.2u; C_1210_3225Metric
C3: 10uF (885012209073); C_1210_3225Metric; Mouser Part Number 710-885012209073
C4: WCAP-AIG8_30X46; WCAP-AIG8_30X46_DXL_
C5: CKG57NX7R2J474M500JH; CAPC6050X550N; Manufacturer_Part_Number CKG57NX7R2J474M500JH
D1: US1M; D_SMA
IC1: LT3751IFE#PBF; SOP65P640X120-21N; Mouser Part Number 584-LT3751IFE#PBF
J1: Conn_01x04_Pin; PinHeader_1x04_P2.54mm_Vertical
J2: Conn_01x03_Pin; PinHeader_1x03_P2.54mm_Vertical
M1: NMOS; TO-263-3_TabPin2
R1.1, R3.1: 1.8k; R_0603_1608Metric
R1.2, R3.2: 68k; R_1206_3216Metric
R2, R4: 475k; R_0603_1608Metric
R3, R8: 40.2k; R_0603_1608Metric
R5: 6m; R_0805_2012Metric
R7.1: 200; R_0805_2012Metric
R7.2: 18k; R_0603_1608Metric
R9: 4.02k; R_0603_1608Metric
R10: 30.9k; R_1206_3216Metric
R11: 383; R_1206_3216Metric
T1: DA2034-ALD; SOP300P3000X1143-12N; Mouser Part Number 994-DA2034-ALD

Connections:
/24V: C1.1 (+), C2.1.1, C2.2.1, C2.3.1, C2.4.1, C2.5.1, C3.1, IC1.13 (VCC), IC1.14 (LVGATE), J1.2, R1.1.2, R2.2, R3.2, R3.1.2, R4.2, T1.3 (PRI_1), T1.4 (PRI_2), T1.5 (PRI_3), T1.6 (PRI_4)
/100V: C4.1, C5.2, D1.1 (K), J2.3, R10.1
/Charge: IC1.8 (CHARGE), J1.4
/Done: IC1.7 (~DONE), J1.3
/GND: C1.2 (-), C2.1, C2.2, C2.1.2, C2.2.2, C2.3.2, C2.4.2, C2.5.2, C3.2, C4.2, C5.1, IC1.9 (CLAMP), IC1.10 (FB), IC1.11 (CSN), J1.1, J2.1, R5.2, R9.2, R10.2, R11.1, R11.2, T1.12 (SEC_2)
unnamed: D1.2 (A), T1.1 (SEC_1)
unnamed: IC1.12 (CSP), M1.3 (S), R5.1
unnamed: IC1.15 (HVGATE), M1.2 (G)
unnamed: IC1.3 (OVLO1), R2.1
unnamed: IC1.5 (OVLO2), R4.1
unnamed: IC1.16 (RBG), R9.1
unnamed: IC1.20 (RDCM), R7.1.1
unnamed: IC1.18 (RVOUT), R8.1
unnamed: IC1.1 (RVTRANS), R3.1
unnamed: IC1.2 (UVLO1), R1.2.1
unnamed: IC1.4 (UVLO2), R3.2.1
unnamed: M1.1 (D), R7.2.2, R8.2, T1.7 (PRI_5), T1.8 (PRI_6), T1.9 (PRI_7), T1.10 (PRI_8)
unnamed: R1.1.1, R1.2.2
unnamed: R3.1.1, R3.2.2
unnamed: R7.1.2, R7.2.1

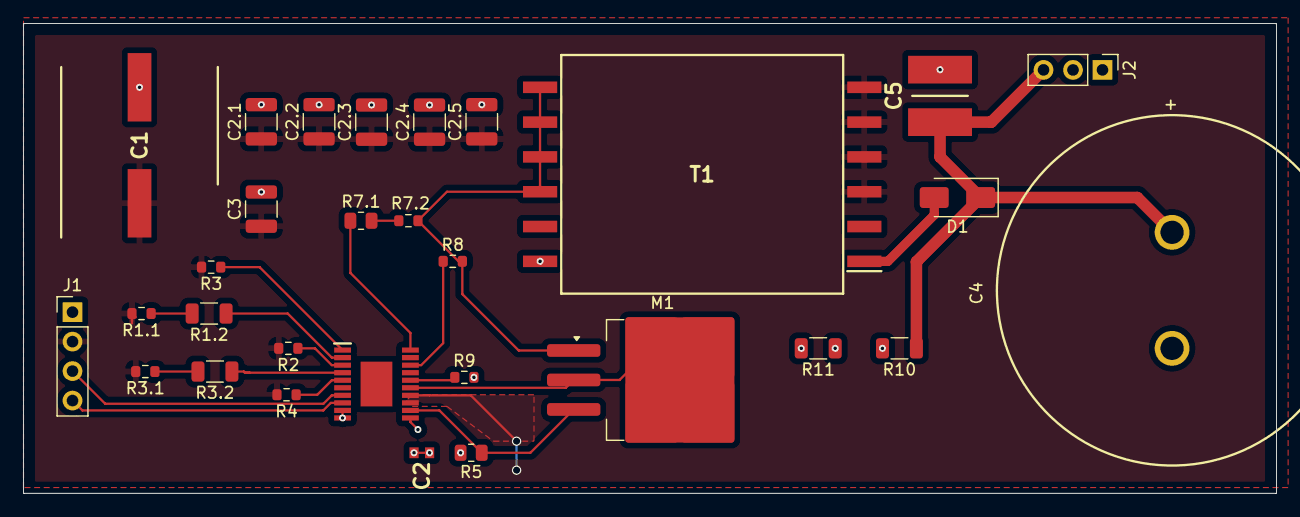
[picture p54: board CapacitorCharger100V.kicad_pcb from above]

Board: 2 copper layers, 108.0 x 40.5 mm, 30 parts (0 on the bottom side), 20 nets.

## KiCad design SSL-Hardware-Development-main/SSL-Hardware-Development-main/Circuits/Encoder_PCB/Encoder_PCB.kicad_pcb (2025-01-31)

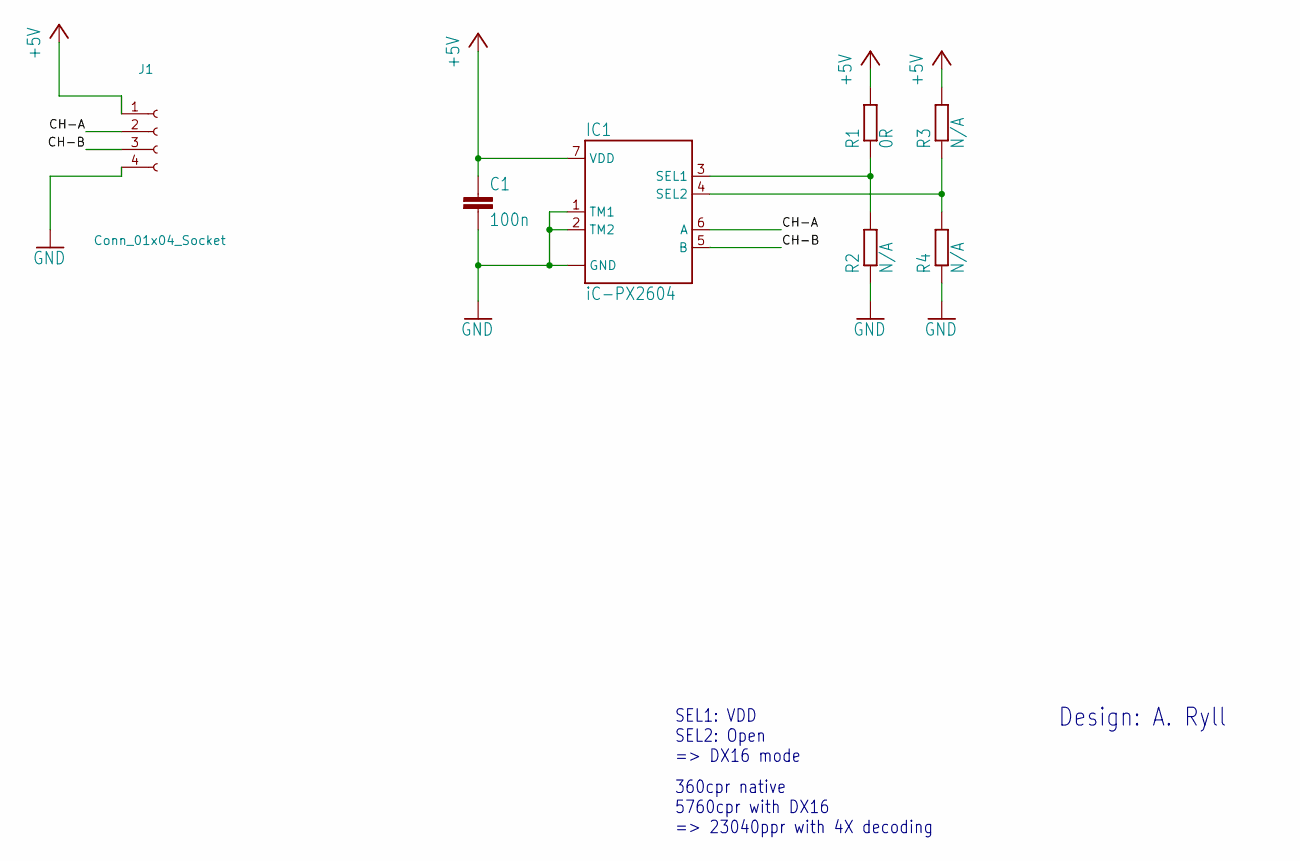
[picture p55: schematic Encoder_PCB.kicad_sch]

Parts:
C1: 100n; C_0603_1608Metric
IC1: iC-PX2604; ODFN8-3X3
J1: Conn_01x04_Socket; PinSocket_1x04_P2.54mm_Vertical
R1: 0R; R_0603_1608Metric
R2, R3, R4: N/A; R_0603_1608Metric

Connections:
+5V: C1.1, IC1.7 (VDD), J1.1, R1.2, R3.2
/CH-A: IC1.6 (A), J1.2
/CH-B: IC1.5 (B), J1.3
GND: C1.2, IC1.1 (TM1), IC1.2 (TM2), IC1.8 (GND), IC1.BP (GND), J1.4, R2.1, R4.1
unnamed: IC1.3 (SEL1), R1.1, R2.2
unnamed: IC1.4 (SEL2), R3.1, R4.2

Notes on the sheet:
360cpr native 5760cpr with DX16 => 23040ppr with 4X decoding
Design: A. Ryll
SEL1: VDD SEL2: Open => DX16 mode

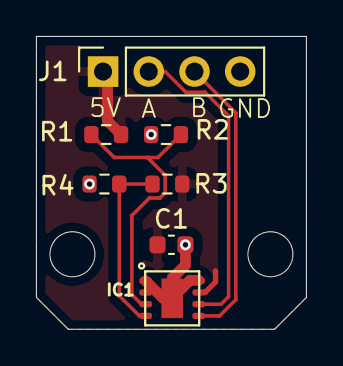
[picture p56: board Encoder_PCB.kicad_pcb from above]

Board: 2 copper layers, 15.0 x 16.3 mm, 7 parts (0 on the bottom side), 6 nets.

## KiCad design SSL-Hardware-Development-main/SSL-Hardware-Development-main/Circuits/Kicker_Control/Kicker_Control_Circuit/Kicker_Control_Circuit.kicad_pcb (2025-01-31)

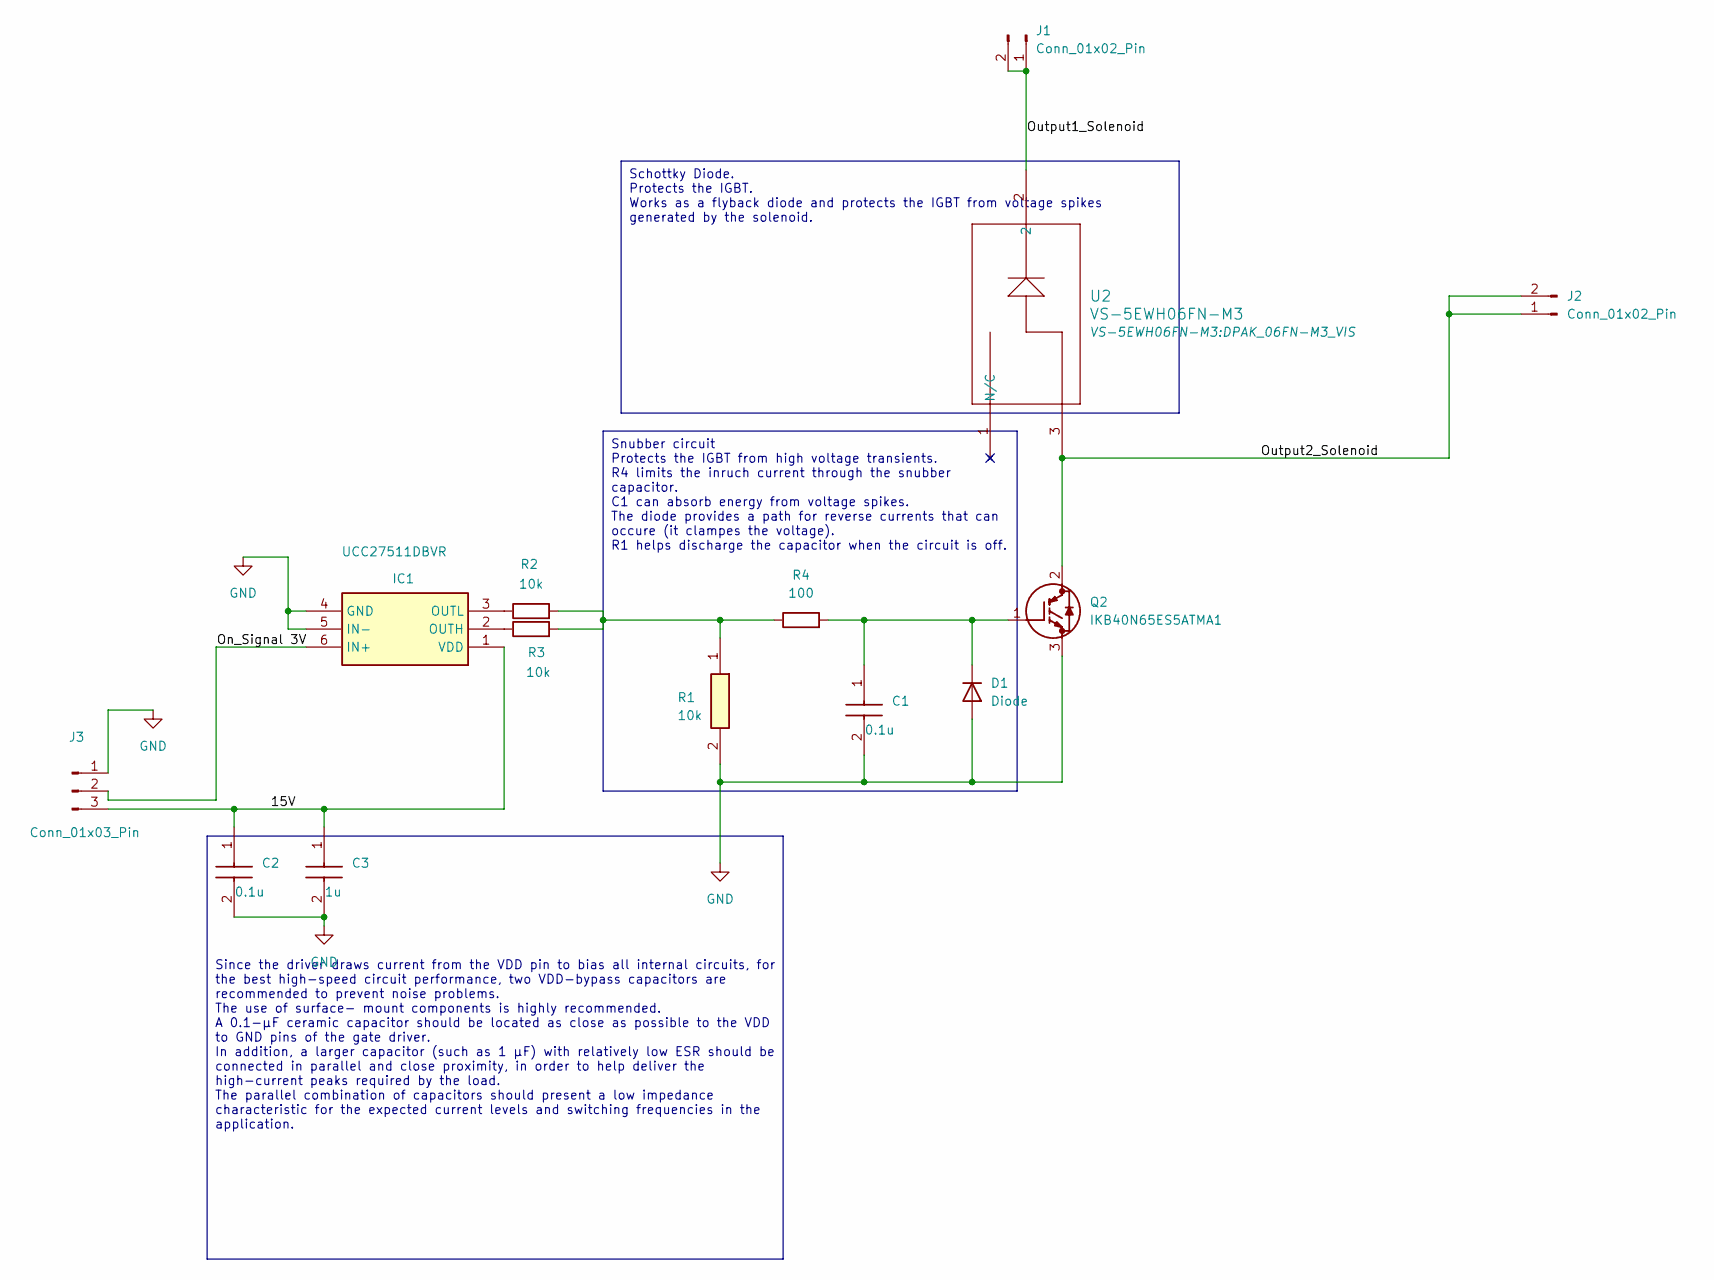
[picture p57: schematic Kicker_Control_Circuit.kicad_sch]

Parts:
C1, C2: 0.1u; C_0805_2012Metric_Pad1.18x1.45mm_HandSolder; Mouser Part Number 871-B32671P6104K000
C3: 1u; C_0805_2012Metric_Pad1.18x1.45mm_HandSolder; Mouser Part Number 871-B32671P6104K000
D1: Diode; D_SMC
IC1: UCC27511DBVR; BTS141TCBUMA1; Mouser Part Number 595-UCC27511DBVR
J1, J2: Conn_01x02_Pin; PinHeader_1x02_P2.54mm_Vertical
J3: Conn_01x03_Pin; PinHeader_1x03_P2.54mm_Vertical
Q2: IKB40N65ES5ATMA1; BTS141TCBUMA1; Mouser Part Number 726-IKB40N65ES5ATMA1
R1: 10k; R_1210_3225Metric; Mouser Part Number 71-CRCW121010K0JNAIF
R2, R3: 10k; R_1210_3225Metric
R4: 100; R_2010_5025Metric
U2: VS-5EWH06FN-M3; DPAK_06FN-M3_VIS

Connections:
/15V: C2.1, C3.1, IC1.1 (VDD), J3.3
/On_Signal 3V: IC1.6 (IN+), J3.2
/Output1_Solenoid: J1.1, J1.2, U2.2
/Output2_Solenoid: J2.1, J2.2, Q2.2 (C), U2.3
GND: C1.2, C2.2, C3.2, D1.2 (A), IC1.4 (GND), IC1.5 (IN-), J3.1, Q2.3 (E), R1.2
unnamed: C1.1, D1.1 (K), Q2.1 (G), R4.2
unnamed: IC1.2 (OUTH), R3.1
unnamed: IC1.3 (OUTL), R2.1
unnamed: R1.1, R2.2, R3.2, R4.1

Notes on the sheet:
Snubber circuit Protects the IGBT from high voltage transients. R4 limits the inruch current through the snubber capacitor. C1 can absorb energy from voltage spikes. The diode provides a path for reverse currents that can occure (it clampes the voltage). R1 helps discharge the capacitor when the ci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
Since the driver draws current from the VDD pin to bias all internal circuits, for the best high-speed circuit performance, two VDD-bypass capacitors are recommended to prevent noise problems. The use of surface- mount components is highly recommended. A 0.1-μF ceramic capacitor should be located a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
Schottky Diode. Protects the IGBT. Works as a flyback diode and protects the IGBT from voltage spikes generated by the solenoid.


Board: 2 copper layers, 38.5 x 33.0 mm, 14 parts (0 on the bottom side), 9 nets.

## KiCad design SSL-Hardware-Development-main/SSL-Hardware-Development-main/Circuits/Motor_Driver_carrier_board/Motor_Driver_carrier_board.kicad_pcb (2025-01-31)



Board: 2 copper layers, 40.2 x 62.7 mm, 21 parts (5 on the bottom side), 15 nets.

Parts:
5V, 5V#2: TestPoint_Pad_1.4x1.4mm; TestPoint_Pad_1.0x1.0mm
+3.3V: TestPoint_Pad_1.4x1.4mm; TestPoint_Pad_1.0x1.0mm
+24V: OUT1; Solder_Pad_5.0x3.0mm
-24V: OUT1; Solder_Pad_5.0x3.0mm
GND: TestPoint_Pad_1.4x1.4mm; TestPoint_Pad_1.0x1.0mm
GND#2, GND#3: TestPoint_Pad_1.4x1.4mm; TestPoint_Pad_1.0x1.0mm
H1, H2, H3: TestPoint_Pad_1.4x1.4mm; TestPoint_Pad_1.0x1.0mm
J3: 61300511121
OUT1, OUT2, OUT3: OUT1; Solder_Pad_5.0x3.0mm
P2: ESC_Adapter_pins_right_angle
PWM: TestPoint_Pad_1.4x1.4mm; TestPoint_Pad_1.0x1.0mm
RX: TestPoint_Pad_1.4x1.4mm; TestPoint_Pad_1.0x1.0mm
SWCLK: TestPoint_Pad_1.4x1.4mm; TestPoint_Pad_1.0x1.0mm
SWDIO: TestPoint_Pad_1.4x1.4mm; TestPoint_Pad_1.0x1.0mm
TX: TestPoint_Pad_1.4x1.4mm; TestPoint_Pad_1.0x1.0mm

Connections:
3.3V: +3.3V.1, J3.3
5V: 5V.1, 5V#2.1, P2.24, P2.27
24V: +24V.1, P2.13, P2.14, P2.15, P2.16
GND: -24V.1, GND.1, GND#2.1, GND#3.1, J3.4, J3.5, P2.17, P2.18, P2.19, P2.20, P2.26, P2.28
H1: H1.1, P2.23
H2: H2.1, P2.21
H3: H3.1, P2.22
OUT1: OUT1.1, P2.1, P2.2, P2.3, P2.4
OUT2: OUT2.1, P2.5, P2.6, P2.7, P2.8
OUT3: OUT3.1, P2.9, P2.10, P2.11, P2.12
PWM: P2.30, PWM.1
RX: P2.25, RX.1
SWCLK: J3.2, SWCLK.1
SWDIO: J3.1, SWDIO.1
TX: P2.29, TX.1

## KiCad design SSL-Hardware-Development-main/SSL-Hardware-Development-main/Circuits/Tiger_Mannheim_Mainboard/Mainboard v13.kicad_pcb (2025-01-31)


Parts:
ANT0: ANT-SMARA; ANT-SMA-RA
C33: 0p5; C0402
C34, C36, C47, C49, C51: 100n; C0603
C35, C37, C48, C50, C52: 1n; C0603
C38: 100p; C0402
C39: 47p; C0402
C40: 0p8; C0402
C41: 1p5; C0402
C42, C44: NA; C0402
C43: 0p6; C0402
C45: 1u; C0603
C46, C53: 10n; C0603
C54, C55: 10u; C0603
IC9: SKY66112; SMCM-22
IC10: SX1280; QFN24L
IC11: LP5907MFX-3.3; SOT23-5L
L5, L6, L7: 120R; L0603
LED3: gr; CHIP-LED0603
Q2: FL520WFMT1; CRYSTAL-7M
R6: 3n; R0402
R7: 2n7; R0402
R8: 3n9; R0402
R9: 1k; R0603
RN9, RN10, RN11: 100; EXB28V

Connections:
+5V: L7.2; also elsewhere on the board
CPS: IC9.15 (CPS), RN11.5 (2)
CRX: IC9.2 (CRX), RN11.7 (2)
CTX: IC9.17 (CTX), RN11.8 (2)
GND: ANT0.GND1 (GND), ANT0.GND2 (GND), ANT0.GND3 (GND), ANT0.GND4 (GND), C34.2, C35.2, C36.2, C37.2, C40.2, C41.2, C42.2, C43.2, C44.2, C45.2, C46.2, C47.2, C48.2, C49.2, C50.2, C51.2, C52.2, C53.2, C54.2, C55.2, IC9.1 (GND@1), IC9.4 (ANT_SEL), IC9.5 (GND@2), IC9.7 (GND@3), IC9.9 (GND@4), IC9.10 (GND@5), IC9.12 (GND@6), IC9.13 (GND@7), IC9.18 (GND@8), IC9.20 (GND@9), IC9.22 (GND@10), IC9.PAD1 (GND@11), IC9.PAD2 (GND@12), IC10.5 (GND@2), IC10.13 (GND@3), IC10.20 (GND@4), IC10.21 (GND@5), IC10.23 (GND@6), IC10.24 (GND@7), IC10.PAD (GND@1), IC11.2 (GND), LED3.C, Q2.2 (GND1), Q2.4 (GND1), RN10.2 (1), RN10.3 (1), RN10.6 (2), RN10.7 (2); also elsewhere on the board
unnamed: LED3.A, R9.1
unnamed: C54.1, IC11.1 (VIN), L7.1
unnamed: IC10.17 (MOSI), RN9.8 (2)
unnamed: IC10.16 (MISO), RN9.7 (2)
unnamed: IC10.18 (SCK), RN9.6 (2)
unnamed: IC10.19 (~CS), RN9.5 (2)
unnamed: IC10.7 (BUSY), RN10.5 (2)
unnamed: IC10.8 (DIO1), RN10.8 (2)
unnamed: IC10.4 (XTB), Q2.3 (2)
unnamed: IC10.6 (XTA), Q2.1
unnamed: C45.1, C46.1, IC10.2 (VDD_IN), IC10.12 (DCC_FB)
unnamed: C53.1, IC10.1 (VR_PA)
unnamed: C38.2, IC9.21 (RFIN)
unnamed: C33.1, C41.1, R6.2, R7.1
unnamed: C33.2, C38.1, C42.1, R7.2
unnamed: C40.1, IC10.22 (RFIO), R6.1
unnamed: C39.1, IC9.8 (ANT1)
unnamed: C39.2, C43.1, R8.1
unnamed: ANT0.C (1), C44.1, R8.2
SPI1-MISO: RN9.2 (1); also elsewhere on the board
SPI1-MOSI: RN9.1; also elsewhere on the board
SPI1-SCK: RN9.3 (1); also elsewhere on the board
WF-3V3: C55.1, IC11.5 (VOUT), L5.1, L6.1, R9.2
WF-BUSY: RN10.4 (1); also elsewhere on the board
WF-CPS: RN11.4 (1); also elsewhere on the board
WF-CRX: RN11.2 (1); also elsewhere on the board
WF-CS: RN9.4 (1); also elsewhere on the board
WF-CTX: RN11.1; also elsewhere on the board
WF-IRQ: RN10.1; also elsewhere on the board
WF-ON: IC11.3 (ON); also elsewhere on the board
WF_3V3FEM: C47.1, C48.1, C49.1, C50.1, C51.1, C52.1, IC9.3 (CSD), IC9.11 (VDD), IC9.14 (VCC2), IC9.16 (VCC1), IC9.19 (CHL), L6.2
WF_3V3SX: C34.1, C35.1, C36.1, C37.1, IC10.3 (~RESET), IC10.11 (V_DIO), IC10.15 (VBAT), L5.2

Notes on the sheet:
Wireless Interface
Design: A. Ryll


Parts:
C1, C2, C3, C6, C7, C8, C9, C10, C11, C12, C13, C14, C15, C16, C17: 100n; C0603
C4, C5: 10u; C0603
IC1: STM32H743ZST; LQFP144-ST
LED1: gr; CHIP-LED0603
LED2: rd; CHIP-LED0603
Q1: ASE-4.000MHZ-LC-T; OSCI-ASE
R1, R2: 1k; R0603
SW1: KT11P4SA3M; BUTTON4

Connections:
+3V3: C1.1, C3.1, C6.1, C7.1, C8.1, C9.1, C10.1, C11.1, C12.1, C13.1, C14.1, C15.1, C16.1, C17.1, IC1.6 (VBAT), IC1.17 (VDD@1), IC1.30 (VDD@2), IC1.32 (VREF+), IC1.33 (VDDA), IC1.39 (VDD@3), IC1.52 (VDD@4), IC1.62 (VDD@5), IC1.72 (VDD@6), IC1.84 (VDD@7), IC1.95 (VUSB), IC1.108 (VDD@9), IC1.121 (VDD@10), IC1.131 (VDD@11), IC1.143 (PDR_ON), IC1.144 (VDD@12), Q1.1 (OE), Q1.4 (VCC), R1.2, R2.2; also elsewhere on the board
DFSDM-CKOUT: IC1.28 (P2); also elsewhere on the board
DFSDM-DATIN0: IC1.27 (P1); also elsewhere on the board
FMC-A7: IC1.53 (P13); also elsewhere on the board
FMC-D0: IC1.85 (P14); also elsewhere on the board
FMC-D1: IC1.86 (P15); also elsewhere on the board
FMC-D2: IC1.114 (P0); also elsewhere on the board
FMC-D3: IC1.115 (P1); also elsewhere on the board
FMC-D4: IC1.58 (P7); also elsewhere on the board
FMC-D5: IC1.59 (P8); also elsewhere on the board
FMC-D6: IC1.60 (P9); also elsewhere on the board
FMC-D7: IC1.63 (P10); also elsewhere on the board
FMC-D8: IC1.64 (P11); also elsewhere on the board
FMC-D9: IC1.65 (P12); also elsewhere on the board
FMC-D10: IC1.66 (P13); also elsewhere on the board
FMC-D11: IC1.67 (P14); also elsewhere on the board
FMC-D12: IC1.68 (P15); also elsewhere on the board
FMC-D13: IC1.77 (P8); also elsewhere on the board
FMC-D14: IC1.78 (P9); also elsewhere on the board
FMC-D15: IC1.79 (P10); also elsewhere on the board
FMC-NE1: IC1.123 (P7); also elsewhere on the board
FMC-NOE: IC1.118 (P4); also elsewhere on the board
FMC-NWE: IC1.119 (P5); also elsewhere on the board
GND: C1.2, C2.2, C3.2, C4.2, C5.2, C6.2, C7.2, C8.2, C9.2, C10.2, C11.2, C12.2, C13.2, C14.2, C15.2, C16.2, C17.2, IC1.16 (GND@1), IC1.31 (VSSA), IC1.38 (GND@2), IC1.51 (GND@3), IC1.61 (GND@4), IC1.83 (GND@5), IC1.94 (GND@6), IC1.107 (GND@7), IC1.120 (GND@8), IC1.130 (GND@9), IC1.138 (BOOT0), Q1.2 (GND), SW1.3 (2), SW1.4 (2); also elsewhere on the board
IDD0: IC1.87 (P2); also elsewhere on the board
IDD1: IC1.88 (P3); also elsewhere on the board
IDD2: IC1.89 (P4); also elsewhere on the board
IDD3: IC1.90 (P5); also elsewhere on the board
IDD4: IC1.91 (P6); also elsewhere on the board
IDD5: IC1.92 (P7); also elsewhere on the board
IDD6: IC1.93 (P8); also elsewhere on the board
IMU-CS: IC1.137 (P7); also elsewhere on the board
IMU-INT: IC1.3 (P4); also elsewhere on the board
JTAG-RESV1: IC1.110 (P15)
JTAG-RESV2: IC1.133 (P3)
JTAG-RESV3: IC1.134 (P4)
KICK-CHG: IC1.126 (P11); also elsewhere on the board
KICK-CS: IC1.127 (P12); also elsewhere on the board
KICK-ERR: IC1.125 (P10); also elsewhere on the board
KILL: IC1.122 (P6); also elsewhere on the board
LCD-ON: IC1.55 (P15); also elsewhere on the board
LCD-RESET: IC1.57 (P1); also elsewhere on the board
LED1: IC1.26 (P0), LED1.C
LED2: IC1.29 (P3), LED2.C
MAG-CS: IC1.7 (P13); also elsewhere on the board
MAG-DRDY: IC1.8 (P14); also elsewhere on the board
MAG-INT: IC1.9 (P15); also elsewhere on the board
unnamed: LED1.A, R1.1
unnamed: LED2.A, R2.1
unnamed: IC1.23 (OSC_IN), Q1.3 (FO)
unnamed: C5.1, IC1.106 (VCAP@2)
unnamed: C4.1, IC1.71 (VCAP@1)
OTG-FS-DM: IC1.103 (P11); also elsewhere on the board
OTG-FS-DP: IC1.104 (P12); also elsewhere on the board
PDN: IC1.117 (P3); also elsewhere on the board
SD-CD: IC1.49 (P11); also elsewhere on the board
SD-PWR: IC1.80 (P11); also elsewhere on the board
SD-WP: IC1.73 (P12); also elsewhere on the board
SDMMC1-CK: IC1.113 (P12); also elsewhere on the board
SDMMC1-CMD: IC1.116 (P2); also elsewhere on the board
SDMMC1-D0: IC1.98 (P8); also elsewhere on the board
SDMMC1-D1: IC1.99 (P9); also elsewhere on the board
SDMMC1-D2: IC1.111 (P10); also elsewhere on the board
SDMMC1-D3: IC1.112 (P11); also elsewhere on the board
SMB-ALRT: IC1.12 (P2); also elsewhere on the board
SMB-RST: IC1.128 (P13); also elsewhere on the board
SMB-SCL: IC1.11 (P1); also elsewhere on the board
SMB-SDA: IC1.10 (P0); also elsewhere on the board
SPI1-MISO: IC1.42 (P6); also elsewhere on the board
SPI1-MOSI: IC1.43 (P7); also elsewhere on the board
SPI1-SCK: IC1.41 (P5); also elsewhere on the board
SPI2-MISO: IC1.75 (P14); also elsewhere on the board
SPI2-MOSI: IC1.76 (P15); also elsewhere on the board
SPI2-SCK: IC1.74 (P13); also elsewhere on the board
SPI4-MISO: IC1.4 (P5); also elsewhere on the board
SPI4-MOSI: IC1.5 (P6); also elsewhere on the board
SPI4-SCK: IC1.1 (P2); also elsewhere on the board
SRST: C2.1, IC1.25 (~RST), SW1.1, SW1.2 (1); also elsewhere on the board
SWCLK: IC1.109 (P14); also elsewhere on the board
SWDIO: IC1.105 (P13); also elsewhere on the board
TIM1-CH1: IC1.100 (P8); also elsewhere on the board
TIM3-CH1: IC1.96 (P6); also elsewhere on the board
TIM3-CH2: IC1.97 (P7); also elsewhere on the board
TIM3-CH3: IC1.46 (P0); also elsewhere on the board
TIM3-CH4: IC1.47 (P1); also elsewhere on the board
TIM4-CH1: IC1.81 (P12); also elsewhere on the board
TIM4-CH2: IC1.82 (P13); also elsewhere on the board
TIM4-CH3: IC1.139 (P8); also elsewhere on the board
TIM4-CH4: IC1.140 (P9); also elsewhere on the board
TIM13-CH1: IC1.20 (P8); also elsewhere on the board
TIM14-CH1: IC1.21 (P9); also elsewhere on the board
TP-CS: IC1.56 (P0); also elsewhere on the board
TP-IRQ: IC1.40 (P4); also elsewhere on the board
UART4-RX: IC1.35 (P1); also elsewhere on the board
UART4-TX: IC1.34 (P0); also elsewhere on the board
UART5-RX: IC1.135 (P5); also elsewhere on the board
UART5-TX: IC1.136 (P6); also elsewhere on the board
UART7-RX: IC1.18 (P6); also elsewhere on the board
UART7-TX: IC1.19 (P7); also elsewhere on the board
UART8-RX: IC1.141 (P0); also elsewhere on the board
UART8-TX: IC1.142 (P1); also elsewhere on the board
USART1-RX: IC1.102 (P10); also elsewhere on the board
USART1-TX: IC1.101 (P9); also elsewhere on the board
USART2-RX: IC1.37 (P3); also elsewhere on the board
USART2-TX: IC1.36 (P2); also elsewhere on the board
USART3-RX: IC1.70 (P11); also elsewhere on the board
USART3-TX: IC1.69 (P10); also elsewhere on the board
USART6-RX: IC1.124 (P9); also elsewhere on the board
USART6-TX: IC1.129 (P14); also elsewhere on the board
USB-ATT: IC1.132 (P15); also elsewhere on the board
USB-EN: IC1.54 (P14); also elsewhere on the board
WF-BUSY: IC1.44 (P4); also elsewhere on the board
WF-CPS: IC1.13 (P3); also elsewhere on the board
WF-CRX: IC1.14 (P4); also elsewhere on the board
WF-CS: IC1.22 (P10); also elsewhere on the board
WF-CTX: IC1.15 (P5); also elsewhere on the board
WF-IRQ: IC1.45 (P5); also elsewhere on the board
WF-ON: IC1.48 (P2); also elsewhere on the board

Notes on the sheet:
Main Processor
Design: A. Ryll

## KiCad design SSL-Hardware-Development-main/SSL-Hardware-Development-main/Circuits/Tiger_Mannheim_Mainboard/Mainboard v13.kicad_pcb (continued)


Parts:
C18, C19, C21, C24, C26, C27, C29, C30, C31: 100n; C0603
C20, C22, C23, C25, C28, C32: 10u; C0603
IC2, IC6: STMPS2151STR; SOT23-5
IC3: LT24
IC4, IC5: MP34DT05; HCLGA4
IC7: ICM-20689; QFN24-4X4-P
IC8: LIS3MDL; VFLGA-12
L1, L2, L3, L4: 120R; L0603
R3, R4: 10k; R0603
RN1, RN2, RN3, RN4, RN5, RN6, RN7, RN8, RN12: 100; EXB28V
SD0: SDCARD
USB0: USBATE; USBA-TE

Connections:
+3V3: C22.1, C23.1, C26.1, C30.1, IC4.1 (VDD), IC4.2 (LR), IC5.1 (VDD), IC7.8 (VDDIO), IC8.6 (VDDIO), L1.2, L2.2, L3.2, L4.2; also elsewhere on the board
+5V: C18.1, C24.1, IC3.11 (VCC5), IC6.5 (IN); also elsewhere on the board
DFSDM-CKOUT: IC4.3 (CLK), IC5.3 (CLK); also elsewhere on the board
DFSDM-DATIN0: IC4.4 (DOUT), IC5.4 (DOUT); also elsewhere on the board
FMC-A7: IC3.15 (RS); also elsewhere on the board
FMC-D0: IC3.9 (D0); also elsewhere on the board
FMC-D1: IC3.8 (D1); also elsewhere on the board
FMC-D2: IC3.7 (D2); also elsewhere on the board
FMC-D3: IC3.6 (D3); also elsewhere on the board
FMC-D4: IC3.16 (D4); also elsewhere on the board
FMC-D5: IC3.17 (D5); also elsewhere on the board
FMC-D6: IC3.18 (D6); also elsewhere on the board
FMC-D7: IC3.19 (D7); also elsewhere on the board
FMC-D8: IC3.20 (D8); also elsewhere on the board
FMC-D9: IC3.21 (D9); also elsewhere on the board
FMC-D10: IC3.22 (D10); also elsewhere on the board
FMC-D11: IC3.23 (D11); also elsewhere on the board
FMC-D12: IC3.24 (D12); also elsewhere on the board
FMC-D13: IC3.25 (D13); also elsewhere on the board
FMC-D14: IC3.26 (D14); also elsewhere on the board
FMC-D15: IC3.27 (D15); also elsewhere on the board
FMC-NE1: IC3.28 (CS); also elsewhere on the board
FMC-NOE: IC3.13 (RD); also elsewhere on the board
FMC-NWE: IC3.14 (WR); also elsewhere on the board
GND: C18.2, C19.2, C20.2, C21.2, C22.2, C23.2, C24.2, C25.2, C26.2, C27.2, C28.2, C29.2, C30.2, C31.2, C32.2, IC2.2 (GND), IC3.12 (GND@1), IC3.30 (GND@2), IC4.G1 (GND), IC4.G2 (GND), IC4.G3 (GND), IC4.G4 (GND), IC5.2 (LR), IC5.G1 (GND), IC5.G2 (GND), IC5.G3 (GND), IC5.G4 (GND), IC6.2 (GND), IC7.11 (FSYNC), IC7.18 (GND), IC8.2 (RSV1), IC8.3 (GND), IC8.12 (RSV2), R3.2, R4.1, RN6.4 (1), RN6.5 (2), RN8.2 (1), RN8.3 (1), RN12.2 (1), RN12.3 (1), RN12.6 (2), RN12.7 (2), SD0.3 (GND@1), SD0.6 (GND@2), SD0.COM1 (COM@1), SD0.COM2 (COM@2), SD0.COM3 (COM@3), SD0.COM4 (COM@4), USB0.4 (GND), USB0.MNT1 (S@1), USB0.MNT2 (S@2); also elsewhere on the board
IMU-CS: RN6.1; also elsewhere on the board
IMU-INT: RN12.4 (1); also elsewhere on the board
LCD-ON: RN4.5 (2); also elsewhere on the board
LCD-RESET: RN4.8 (2); also elsewhere on the board
MAG-CS: RN7.2 (1); also elsewhere on the board
MAG-DRDY: RN8.4 (1); also elsewhere on the board
MAG-INT: RN8.1; also elsewhere on the board
unnamed: IC8.10 (~CS), RN7.7 (2)
unnamed: IC8.1 (SCL/SCLK), RN7.5 (2)
unnamed: IC8.11 (SDA/MOSI), RN7.6 (2)
unnamed: IC8.9 (SA1/MISO), RN7.8 (2)
unnamed: IC8.7 (INT), RN8.8 (2)
unnamed: IC8.8 (DRDY), RN8.5 (2)
unnamed: C29.1, IC8.4 (C1)
unnamed: C31.1, C32.1, IC8.5 (VDD), L4.1
unnamed: IC7.12 (INT), RN12.5 (2)
unnamed: C19.1, IC3.29 (VCC3.3), L1.1
unnamed: IC3.38 (RESET), RN4.1
unnamed: IC3.40 (LCD_ON), RN4.4 (1)
unnamed: IC3.1 (TP_IRQ), RN1.2 (1)
unnamed: IC3.39 (TP_CS), RN4.3 (1)
unnamed: IC3.5 (TP_CLK), RN1.4 (1)
unnamed: IC3.2 (TP_DOUT), RN1.1
unnamed: IC3.4 (TP_DIN), RN1.3 (1)
unnamed: RN2.7 (2), SD0.8 (D1)
unnamed: RN2.8 (2), SD0.7 (D0)
unnamed: RN3.5 (2), SD0.5 (CLK)
unnamed: RN3.6 (2), SD0.2 (CMD)
unnamed: RN3.8 (2), SD0.9 (D2)
unnamed: RN3.7 (2), SD0.1 (D3)
unnamed: RN2.6 (2), SD0.CD
unnamed: RN2.5 (2), SD0.WP
unnamed: C20.1, C21.1, IC2.5 (IN), L2.1
unnamed: IC6.1 (OUT), USB0.1 (+5V)
unnamed: RN5.5 (2), USB0.2 (D-)
unnamed: RN5.8 (2), USB0.3 (D+)
unnamed: IC7.9 (AD0/SDO), RN12.8 (2)
unnamed: C25.1, IC7.10 (REGOUT)
unnamed: C27.1, C28.1, IC7.13 (VDD), L3.1
unnamed: IC7.24 (SDA/SDI), RN6.6 (2)
unnamed: IC7.23 (SCL/SCLK), RN6.7 (2)
unnamed: IC7.22 (~CS), RN6.8 (2)
OTG-FS-DM: RN5.4 (1); also elsewhere on the board
OTG-FS-DP: RN5.1; also elsewhere on the board
SD-CD: RN2.3 (1); also elsewhere on the board
SD-PWR: IC2.4 (EN), R3.1; also elsewhere on the board
SD-WP: RN2.4 (1); also elsewhere on the board
SDMMC1-CK: RN3.4 (1); also elsewhere on the board
SDMMC1-CMD: RN3.3 (1); also elsewhere on the board
SDMMC1-D0: RN2.1; also elsewhere on the board
SDMMC1-D1: RN2.2 (1); also elsewhere on the board
SDMMC1-D2: RN3.1; also elsewhere on the board
SDMMC1-D3: RN3.2 (1); also elsewhere on the board
SD_PWR: IC2.1 (OUT), SD0.4 (VDD)
SPI4-MISO: RN1.8 (2), RN7.1, RN12.1; also elsewhere on the board
SPI4-MOSI: RN1.6 (2), RN6.3 (1), RN7.3 (1); also elsewhere on the board
SPI4-SCK: RN1.5 (2), RN6.2 (1), RN7.4 (1); also elsewhere on the board
TP-CS: RN4.6 (2); also elsewhere on the board
TP-IRQ: RN1.7 (2); also elsewhere on the board
USB-EN: IC6.4 (EN), R4.2; also elsewhere on the board

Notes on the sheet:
2mA
IMU
Design: A. Ryll
USB Host
SD Card
Magnetometer
Microphones
LCD


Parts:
C56, C58: 33u; C1206; VOLTAGE 25V
C57, C59: 100n; C0603
IC12: LT3080ST; SOT223
IDD0: TE-FPC-1MM-8V; TE-1734248-8
L8: 470R; L1206
LED4: gr; CHIP-LED0603
LEDS0: TE-FPC-1MM-10H; TE-1-84952-0
PAD1, PAD2, PAD3: WIREPAD5,4/3,0; 5,4_3,0
PWR0: 4-1734742-0; TE-4-1734592-0
R10: 1k; R0603
R11: 330k; R0603
SW2: KT11P4SA3M; KT11

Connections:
+3V3: C58.1, IC12.2 (OUT), IC12.4 (OUT), R10.2; also elsewhere on the board
+5V: L8.1, LEDS0.1, PWR0.1, PWR0.2; also elsewhere on the board
BTN: PWR0.18, SW2.1
GND: C56.2, C57.2, C58.2, C59.2, LED4.C, LEDS0.10, PAD1.1, PAD1.2, PAD2.1, PAD2.2, PAD3.1, PAD3.2, PWR0.39, PWR0.40, R11.1, SW2.2; also elsewhere on the board
IDD0: IDD0.A2, IDD0.B2; also elsewhere on the board
IDD1: IDD0.A3, IDD0.B3; also elsewhere on the board
IDD2: IDD0.A4, IDD0.B4; also elsewhere on the board
IDD3: IDD0.A5, IDD0.B5; also elsewhere on the board
IDD4: IDD0.A6, IDD0.B6; also elsewhere on the board
IDD5: IDD0.A7, IDD0.B7; also elsewhere on the board
IDD6: IDD0.A8, IDD0.B8; also elsewhere on the board
KICK-CHG: PWR0.35; also elsewhere on the board
KICK-CS: PWR0.31; also elsewhere on the board
KICK-ERR: PWR0.38; also elsewhere on the board
KILL: PWR0.17; also elsewhere on the board
unnamed: C59.1, IC12.1 (SET), R11.2
unnamed: LED4.A, R10.1
unnamed: C56.1, C57.1, IC12.3 (IN), L8.2
PDN: PWR0.19; also elsewhere on the board
SMB-ALRT: PWR0.13; also elsewhere on the board
SMB-RST: PWR0.12; also elsewhere on the board
SMB-SCL: PWR0.15; also elsewhere on the board
SMB-SDA: PWR0.14; also elsewhere on the board
SPI2-MISO: PWR0.33; also elsewhere on the board
SPI2-MOSI: PWR0.32; also elsewhere on the board
SPI2-SCK: PWR0.34; also elsewhere on the board
SRST: PWR0.28; also elsewhere on the board
SWCLK: PWR0.26; also elsewhere on the board
SWDIO: PWR0.27; also elsewhere on the board
TIM1-CH1: PWR0.16; also elsewhere on the board
TIM3-CH1: LEDS0.2; also elsewhere on the board
TIM3-CH2: LEDS0.3; also elsewhere on the board
TIM3-CH3: LEDS0.4; also elsewhere on the board
TIM3-CH4: LEDS0.5; also elsewhere on the board
TIM4-CH1: LEDS0.6; also elsewhere on the board
TIM4-CH2: LEDS0.7; also elsewhere on the board
TIM4-CH3: LEDS0.8; also elsewhere on the board
TIM4-CH4: LEDS0.9; also elsewhere on the board
TIM13-CH1: PWR0.36; also elsewhere on the board
TIM14-CH1: PWR0.37; also elsewhere on the board
UART4-RX: PWR0.9; also elsewhere on the board
UART4-TX: PWR0.10; also elsewhere on the board
UART5-RX: PWR0.5; also elsewhere on the board
UART5-TX: PWR0.6; also elsewhere on the board
UART7-RX: PWR0.7; also elsewhere on the board
UART7-TX: PWR0.8; also elsewhere on the board
UART8-RX: PWR0.3; also elsewhere on the board
UART8-TX: PWR0.4; also elsewhere on the board
USART1-RX: PWR0.30; also elsewhere on the board
USART1-TX: PWR0.29; also elsewhere on the board
USART2-RX: PWR0.23; also elsewhere on the board
USART2-TX: PWR0.22; also elsewhere on the board
USART3-RX: PWR0.21; also elsewhere on the board
USART3-TX: PWR0.20; also elsewhere on the board
USART6-RX: PWR0.24; also elsewhere on the board
USART6-TX: PWR0.25; also elsewhere on the board
USB-ATT: PWR0.11; also elsewhere on the board

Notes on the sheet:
Max output: 800mA (110°C)
LDO 3.3V
Connectors
Kicker
DIS1
DIS2
Design: A. Ryll
Buzzer



Board: 4 copper layers, 80.0 x 85.0 mm, 118 parts (3 on the bottom side), 181 nets.

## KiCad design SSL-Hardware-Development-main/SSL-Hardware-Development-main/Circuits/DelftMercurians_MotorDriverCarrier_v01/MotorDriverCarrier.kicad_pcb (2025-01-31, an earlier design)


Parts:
C0: C_Polarized; CP_Radial_D8.0mm_P3.50mm
C1: 0.1u; C_0603_1608Metric_Pad1.08x0.95mm_HandSolder
D1, D2, D3, D5: LED; LED_0603_1608Metric_Pad1.05x0.95mm_HandSolder
D4: BZV55C15; D_MiniMELF
H1: MountingHole; MountingHole_3.2mm_M3_ISO14580
H2: VIN; MountingHole_3.2mm_M3_ISO7380_Pad_TopOnly
H3: PGND; MountingHole_3.2mm_M3_ISO7380_Pad_TopOnly
J1: Motor_Encoder; PinHeader_2x05_P1.27mm_Vertical
J2: Driver_Encoder; PinHeader_1x05_P1.27mm_Vertical
J3, J4, J5, J6, J7: Conn_01x01_Male; PinHeader_1x01_P2.54mm_Vertical
J8: CAN_1; JST_GH_SM03B-GHS-TB_1x03-1MP_P1.25mm_Horizontal
J9: CAN_2; JST_GH_SM03B-GHS-TB_1x03-1MP_P1.25mm_Horizontal
J10: Edge_Motor; CustomEdge_Motor3
J11: Edge_Power; CustomEdge_Power2
J12: UART_1; JST_GH_SM04B-GHS-TB_1x04-1MP_P1.25mm_Horizontal
J13: Edge_UART; CustomEdge_UART5
J14: Edge_CAN; CustomEdge_CAN4
JP1: Jumper_2_Bridged; SolderJumper-2_P1.3mm_Open_TrianglePad1.0x1.5mm
JP2, JP3: Jumper_2_Open; SolderJumper-2_P1.3mm_Open_RoundedPad1.0x1.5mm
Q1: 671-1100; SOT-223-3_TabPin2
R1, R2: 1k5; R_0603_1608Metric_Pad0.98x0.95mm_HandSolder
R3, R4, R5: R10k; R_0603_1608Metric_Pad0.98x0.95mm_HandSolder
R6: 11k; R_0603_1608Metric_Pad0.98x0.95mm_HandSolder
R7: 1k8; R_0603_1608Metric_Pad0.98x0.95mm_HandSolder
U1: UA9637; SOIC-8_3.9x4.9mm_P1.27mm

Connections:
+5V: C1.1, J1.10, J4.1, J14.4, JP2.1 (A), R1.1, R3.1, U1.1 (VCC)
+24V: C0.1, D4.1 (K), J11.2, Q1.3 (S)
/Vin: H2.1, Q1.2 (D), Q1.4 (D), R6.1
A: J2.5, U1.2 (OUT)
A+: J1.8, U1.8 (IN+)
A-: J1.9, U1.7 (IN-)
B: J2.4, U1.3 (OUT)
B+: J1.6, U1.6 (IN+)
B-: J1.7, U1.5 (IN-)
CAN_H: J8.3, J9.3, J14.2
CAN_L: J8.2, J9.2, J14.3
ENCODER_HOUSING: J1.2
GND: C1.2, D1.1 (K), D2.1 (K), J1.1, J6.1, J8.1, J9.1, J14.1, JP1.2 (B), JP3.1 (A), R5.2, U1.4 (GND)
GNDPWR: C0.2, D3.1 (K), D5.2 (A), H3.1, J11.1, J12.MP (MountPin), JP1.1 (A), R7.2
H1: J1.5
H2: J1.4
H3: J1.3
MOTOR_A: J10.1
MOTOR_B: J10.2
MOTOR_C: J10.3
unnamed: D1.2 (A), R1.2
unnamed: D2.2 (A), R2.2
unnamed: D3.2 (A), D5.1 (K), R6.2
unnamed: D4.2 (A), Q1.1 (G), R7.1
unnamed: J2.1, JP3.2 (B)
unnamed: J2.2, JP2.2 (B)
unnamed: J5.1, R3.2, R4.1
unnamed: J7.1, R4.2, R5.1
PWM: J3.1, J13.2
UART_GND: J12.4, J13.1
UART_RX: J12.3, J13.3
UART_TX: J12.2, J13.4, R2.1
UART_VCC: J12.1, J13.5
Z: J2.3

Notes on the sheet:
Daughterboard
CAN Connectors
ID Select
UART Connector
Internals
Encoder Connector
Status LEDs
Line Receiver
Ground Interconnect
Power Input
Outputs
Inputs



Board: 2 copper layers, 46.2 x 61.4 mm, 36 parts (10 on the bottom side), 26 nets.

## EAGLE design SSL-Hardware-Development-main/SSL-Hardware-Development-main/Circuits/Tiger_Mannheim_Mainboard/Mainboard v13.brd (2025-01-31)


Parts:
C1, C2, C3, C6, C7, C8, C9, C10, C11, C12, C13, C14, C15, C16, C17: 100n; C0603
C4, C5: 10u; C0603
IC1: STM32H743ZST; LQFP144-ST
LED1: gr; CHIP-LED0603
LED2: rd; CHIP-LED0603
Q1: ASE-4.000MHZ-LC-T; OSCI-ASE
R1, R2: 1k; R0603
SW1: KT11P4SA3M; BUTTON4

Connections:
+3V3: C1.1, C3.1, C6.1, C7.1, C8.1, C9.1, C10.1, C11.1, C12.1, C13.1, C14.1, C15.1, C16.1, C17.1, IC1.6 (VBAT), IC1.17 (VDD), IC1.30 (VDD), IC1.32 (VREF+), IC1.33 (VDDA), IC1.39 (VDD), IC1.52 (VDD), IC1.62 (VDD), IC1.72 (VDD), IC1.84 (VDD), IC1.95 (VUSB), IC1.108 (VDD), IC1.121 (VDD), IC1.131 (VDD), IC1.143 (PDR_ON), IC1.144 (VDD), Q1.1 (OE), Q1.4 (VCC), R1.2, R2.2; also elsewhere on the board
DFSDM-CKOUT: IC1.28 (P2); also elsewhere on the board
DFSDM-DATIN0: IC1.27 (P1); also elsewhere on the board
FMC-A7: IC1.53 (P13); also elsewhere on the board
FMC-D0: IC1.85 (P14); also elsewhere on the board
FMC-D1: IC1.86 (P15); also elsewhere on the board
FMC-D2: IC1.114 (P0); also elsewhere on the board
FMC-D3: IC1.115 (P1); also elsewhere on the board
FMC-D4: IC1.58 (P7); also elsewhere on the board
FMC-D5: IC1.59 (P8); also elsewhere on the board
FMC-D6: IC1.60 (P9); also elsewhere on the board
FMC-D7: IC1.63 (P10); also elsewhere on the board
FMC-D8: IC1.64 (P11); also elsewhere on the board
FMC-D9: IC1.65 (P12); also elsewhere on the board
FMC-D10: IC1.66 (P13); also elsewhere on the board
FMC-D11: IC1.67 (P14); also elsewhere on the board
FMC-D12: IC1.68 (P15); also elsewhere on the board
FMC-D13: IC1.77 (P8); also elsewhere on the board
FMC-D14: IC1.78 (P9); also elsewhere on the board
FMC-D15: IC1.79 (P10); also elsewhere on the board
FMC-NE1: IC1.123 (P7); also elsewhere on the board
FMC-NOE: IC1.118 (P4); also elsewhere on the board
FMC-NWE: IC1.119 (P5); also elsewhere on the board
GND: C1.2, C2.2, C3.2, C4.2, C5.2, C6.2, C7.2, C8.2, C9.2, C10.2, C11.2, C12.2, C13.2, C14.2, C15.2, C16.2, C17.2, IC1.16 (GND), IC1.31 (VSSA), IC1.38 (GND), IC1.51 (GND), IC1.61 (GND), IC1.83 (GND), IC1.94 (GND), IC1.107 (GND), IC1.120 (GND), IC1.130 (GND), IC1.138 (BOOT0), Q1.2 (GND), SW1.3 (2), SW1.4 (2); also elsewhere on the board
IDD0: IC1.87 (P2); also elsewhere on the board
IDD1: IC1.88 (P3); also elsewhere on the board
IDD2: IC1.89 (P4); also elsewhere on the board
IDD3: IC1.90 (P5); also elsewhere on the board
IDD4: IC1.91 (P6); also elsewhere on the board
IDD5: IC1.92 (P7); also elsewhere on the board
IDD6: IC1.93 (P8); also elsewhere on the board
IMU-CS: IC1.137 (P7); also elsewhere on the board
IMU-INT: IC1.3 (P4); also elsewhere on the board
JTAG-RESV1: IC1.110 (P15)
JTAG-RESV2: IC1.133 (P3)
JTAG-RESV3: IC1.134 (P4)
KICK-CHG: IC1.126 (P11); also elsewhere on the board
KICK-CS: IC1.127 (P12); also elsewhere on the board
KICK-ERR: IC1.125 (P10); also elsewhere on the board
KILL: IC1.122 (P6); also elsewhere on the board
LCD-ON: IC1.55 (P15); also elsewhere on the board
LCD-RESET: IC1.57 (P1); also elsewhere on the board
LED1: IC1.26 (P0), LED1.C
LED2: IC1.29 (P3), LED2.C
MAG-CS: IC1.7 (P13); also elsewhere on the board
MAG-DRDY: IC1.8 (P14); also elsewhere on the board
MAG-INT: IC1.9 (P15); also elsewhere on the board
unnamed: LED1.A, R1.1
unnamed: LED2.A, R2.1
unnamed: IC1.23 (OSC_IN), Q1.3 (FO)
unnamed: C5.1, IC1.106 (VCAP)
unnamed: C4.1, IC1.71 (VCAP)
OTG-FS-DM: IC1.103 (P11); also elsewhere on the board
OTG-FS-DP: IC1.104 (P12); also elsewhere on the board
PDN: IC1.117 (P3); also elsewhere on the board
SD-CD: IC1.49 (P11); also elsewhere on the board
SD-PWR: IC1.80 (P11); also elsewhere on the board
SD-WP: IC1.73 (P12); also elsewhere on the board
SDMMC1-CK: IC1.113 (P12); also elsewhere on the board
SDMMC1-CMD: IC1.116 (P2); also elsewhere on the board
SDMMC1-D0: IC1.98 (P8); also elsewhere on the board
SDMMC1-D1: IC1.99 (P9); also elsewhere on the board
SDMMC1-D2: IC1.111 (P10); also elsewhere on the board
SDMMC1-D3: IC1.112 (P11); also elsewhere on the board
SMB-ALRT: IC1.12 (P2); also elsewhere on the board
SMB-RST: IC1.128 (P13); also elsewhere on the board
SMB-SCL: IC1.11 (P1); also elsewhere on the board
SMB-SDA: IC1.10 (P0); also elsewhere on the board
SPI1-MISO: IC1.42 (P6); also elsewhere on the board
SPI1-MOSI: IC1.43 (P7); also elsewhere on the board
SPI1-SCK: IC1.41 (P5); also elsewhere on the board
SPI2-MISO: IC1.75 (P14); also elsewhere on the board
SPI2-MOSI: IC1.76 (P15); also elsewhere on the board
SPI2-SCK: IC1.74 (P13); also elsewhere on the board
SPI4-MISO: IC1.4 (P5); also elsewhere on the board
SPI4-MOSI: IC1.5 (P6); also elsewhere on the board
SPI4-SCK: IC1.1 (P2); also elsewhere on the board
SRST: C2.1, IC1.25 (!RST), SW1.1, SW1.2 (1); also elsewhere on the board
SWCLK: IC1.109 (P14); also elsewhere on the board
SWDIO: IC1.105 (P13); also elsewhere on the board
TIM1-CH1: IC1.100 (P8); also elsewhere on the board
TIM3-CH1: IC1.96 (P6); also elsewhere on the board
TIM3-CH2: IC1.97 (P7); also elsewhere on the board
TIM3-CH3: IC1.46 (P0); also elsewhere on the board
TIM3-CH4: IC1.47 (P1); also elsewhere on the board
TIM4-CH1: IC1.81 (P12); also elsewhere on the board
TIM4-CH2: IC1.82 (P13); also elsewhere on the board
TIM4-CH3: IC1.139 (P8); also elsewhere on the board
TIM4-CH4: IC1.140 (P9); also elsewhere on the board
TIM13-CH1: IC1.20 (P8); also elsewhere on the board
TIM14-CH1: IC1.21 (P9); also elsewhere on the board
TP-CS: IC1.56 (P0); also elsewhere on the board
TP-IRQ: IC1.40 (P4); also elsewhere on the board
UART4-RX: IC1.35 (P1); also elsewhere on the board
UART4-TX: IC1.34 (P0); also elsewhere on the board
UART5-RX: IC1.135 (P5); also elsewhere on the board
UART5-TX: IC1.136 (P6); also elsewhere on the board
UART7-RX: IC1.18 (P6); also elsewhere on the board
UART7-TX: IC1.19 (P7); also elsewhere on the board
UART8-RX: IC1.141 (P0); also elsewhere on the board
UART8-TX: IC1.142 (P1); also elsewhere on the board
USART1-RX: IC1.102 (P10); also elsewhere on the board
USART1-TX: IC1.101 (P9); also elsewhere on the board
USART2-RX: IC1.37 (P3); also elsewhere on the board
USART2-TX: IC1.36 (P2); also elsewhere on the board
USART3-RX: IC1.70 (P11); also elsewhere on the board
USART3-TX: IC1.69 (P10); also elsewhere on the board
USART6-RX: IC1.124 (P9); also elsewhere on the board
USART6-TX: IC1.129 (P14); also elsewhere on the board
USB-ATT: IC1.132 (P15); also elsewhere on the board
USB-EN: IC1.54 (P14); also elsewhere on the board
WF-BUSY: IC1.44 (P4); also elsewhere on the board
WF-CPS: IC1.13 (P3); also elsewhere on the board
WF-CRX: IC1.14 (P4); also elsewhere on the board
WF-CS: IC1.22 (P10); also elsewhere on the board
WF-CTX: IC1.15 (P5); also elsewhere on the board
WF-IRQ: IC1.45 (P5); also elsewhere on the board
WF-ON: IC1.48 (P2); also elsewhere on the board

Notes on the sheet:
Design: A. Ryll
Main Processor


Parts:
C18, C19, C21, C24, C26, C27, C29, C30, C31: 100n; C0603
C20, C22, C23, C25, C28, C32: 10u; C0603
IC2, IC6: STMPS2151STR; SOT23-5
IC3: LT24
IC4, IC5: MP34DT05; HCLGA4
IC7: ICM-20689; QFN24-4X4-P
IC8: LIS3MDL; VFLGA-12
L1, L2, L3, L4: 120R; L0603
R3, R4: 10k; R0603
RN1, RN2, RN3, RN4, RN5, RN6, RN7, RN8, RN12: 100; EXB28V
SD: SDCARD
USB: USBATE; USBA-TE

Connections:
+3V3: C22.1, C23.1, C26.1, C30.1, IC4.1 (VDD), IC4.2 (LR), IC5.1 (VDD), IC7.8 (VDDIO), IC8.6 (VDDIO), L1.2, L2.2, L3.2, L4.2; also elsewhere on the board
+5V: C18.1, C24.1, IC3.11 (VCC5), IC6.5 (IN); also elsewhere on the board
DFSDM-CKOUT: IC4.3 (CLK), IC5.3 (CLK); also elsewhere on the board
DFSDM-DATIN0: IC4.4 (DOUT), IC5.4 (DOUT); also elsewhere on the board
FMC-A7: IC3.15 (RS); also elsewhere on the board
FMC-D0: IC3.9 (D0); also elsewhere on the board
FMC-D1: IC3.8 (D1); also elsewhere on the board
FMC-D2: IC3.7 (D2); also elsewhere on the board
FMC-D3: IC3.6 (D3); also elsewhere on the board
FMC-D4: IC3.16 (D4); also elsewhere on the board
FMC-D5: IC3.17 (D5); also elsewhere on the board
FMC-D6: IC3.18 (D6); also elsewhere on the board
FMC-D7: IC3.19 (D7); also elsewhere on the board
FMC-D8: IC3.20 (D8); also elsewhere on the board
FMC-D9: IC3.21 (D9); also elsewhere on the board
FMC-D10: IC3.22 (D10); also elsewhere on the board
FMC-D11: IC3.23 (D11); also elsewhere on the board
FMC-D12: IC3.24 (D12); also elsewhere on the board
FMC-D13: IC3.25 (D13); also elsewhere on the board
FMC-D14: IC3.26 (D14); also elsewhere on the board
FMC-D15: IC3.27 (D15); also elsewhere on the board
FMC-NE1: IC3.28 (CS); also elsewhere on the board
FMC-NOE: IC3.13 (RD); also elsewhere on the board
FMC-NWE: IC3.14 (WR); also elsewhere on the board
GND: C18.2, C19.2, C20.2, C21.2, C22.2, C23.2, C24.2, C25.2, C26.2, C27.2, C28.2, C29.2, C30.2, C31.2, C32.2, IC2.2 (GND), IC3.12 (GND), IC3.30 (GND), IC4.G1 (GND), IC4.G2 (GND), IC4.G3 (GND), IC4.G4 (GND), IC5.2 (LR), IC5.G1 (GND), IC5.G2 (GND), IC5.G3 (GND), IC5.G4 (GND), IC6.2 (GND), IC7.11 (FSYNC), IC7.18 (GND), IC8.2 (RSV1), IC8.3 (GND), IC8.12 (RSV2), R3.2, R4.1, RN6.4 (1), RN6.5 (2), RN8.2 (1), RN8.3 (1), RN12.2 (1), RN12.3 (1), RN12.6 (2), RN12.7 (2), SD.3 (GND), SD.6 (GND), SD.COM1 (COM), SD.COM2 (COM), SD.COM3 (COM), SD.COM4 (COM), USB.4 (GND), USB.MNT1 (S), USB.MNT2 (S); also elsewhere on the board
IMU-CS: RN6.1; also elsewhere on the board
IMU-INT: RN12.4 (1); also elsewhere on the board
LCD-ON: RN4.5 (2); also elsewhere on the board
LCD-RESET: RN4.8 (2); also elsewhere on the board
MAG-CS: RN7.2 (1); also elsewhere on the board
MAG-DRDY: RN8.4 (1); also elsewhere on the board
MAG-INT: RN8.1; also elsewhere on the board
unnamed: IC8.10 (!CS), RN7.7 (2)
unnamed: IC8.1 (SCL/SCLK), RN7.5 (2)
unnamed: IC8.11 (SDA/MOSI), RN7.6 (2)
unnamed: IC8.9 (SA1/MISO), RN7.8 (2)
unnamed: IC8.7 (INT), RN8.8 (2)
unnamed: IC8.8 (DRDY), RN8.5 (2)
unnamed: C29.1, IC8.4 (C1)
unnamed: C31.1, C32.1, IC8.5 (VDD), L4.1
unnamed: IC7.12 (INT), RN12.5 (2)
unnamed: C19.1, IC3.29 (VCC3.3), L1.1
unnamed: IC3.38 (RESET), RN4.1
unnamed: IC3.40 (LCD_ON), RN4.4 (1)
unnamed: IC3.1 (TP_IRQ), RN1.2 (1)
unnamed: IC3.39 (TP_CS), RN4.3 (1)
unnamed: IC3.5 (TP_CLK), RN1.4 (1)
unnamed: IC3.2 (TP_DOUT), RN1.1
unnamed: IC3.4 (TP_DIN), RN1.3 (1)
unnamed: RN2.7 (2), SD.8 (D1)
unnamed: RN2.8 (2), SD.7 (D0)
unnamed: RN3.5 (2), SD.5 (CLK)
unnamed: RN3.6 (2), SD.2 (CMD)
unnamed: RN3.8 (2), SD.9 (D2)
unnamed: RN3.7 (2), SD.1 (D3)
unnamed: RN2.6 (2), SD.CD
unnamed: RN2.5 (2), SD.WP
unnamed: C20.1, C21.1, IC2.5 (IN), L2.1
unnamed: IC6.1 (OUT), USB.1 (+5V)
unnamed: RN5.5 (2), USB.2 (D-)
unnamed: RN5.8 (2), USB.3 (D+)
unnamed: IC7.9 (AD0/SDO), RN12.8 (2)
unnamed: C25.1, IC7.10 (REGOUT)
unnamed: C27.1, C28.1, IC7.13 (VDD), L3.1
unnamed: IC7.24 (SDA/SDI), RN6.6 (2)
unnamed: IC7.23 (SCL/SCLK), RN6.7 (2)
unnamed: IC7.22 (!CS), RN6.8 (2)
OTG-FS-DM: RN5.4 (1); also elsewhere on the board
OTG-FS-DP: RN5.1; also elsewhere on the board
SD-CD: RN2.3 (1); also elsewhere on the board
SD-PWR: IC2.4 (EN), R3.1; also elsewhere on the board
SD-WP: RN2.4 (1); also elsewhere on the board
SDMMC1-CK: RN3.4 (1); also elsewhere on the board
SDMMC1-CMD: RN3.3 (1); also elsewhere on the board
SDMMC1-D0: RN2.1; also elsewhere on the board
SDMMC1-D1: RN2.2 (1); also elsewhere on the board
SDMMC1-D2: RN3.1; also elsewhere on the board
SDMMC1-D3: RN3.2 (1); also elsewhere on the board
SD_PWR: IC2.1 (OUT), SD.4 (VDD)
SPI4-MISO: RN1.8 (2), RN7.1, RN12.1; also elsewhere on the board
SPI4-MOSI: RN1.6 (2), RN6.3 (1), RN7.3 (1); also elsewhere on the board
SPI4-SCK: RN1.5 (2), RN6.2 (1), RN7.4 (1); also elsewhere on the board
TP-CS: RN4.6 (2); also elsewhere on the board
TP-IRQ: RN1.7 (2); also elsewhere on the board
USB-EN: IC6.4 (EN), R4.2; also elsewhere on the board

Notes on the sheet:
Design: A. Ryll
LCD
Microphones
SD Card
USB Host
Magnetometer
IMU


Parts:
ANT: ANT-SMARA; ANT-SMA-RA
C33: 0p5; C0402
C34, C36, C47, C49, C51: 100n; C0603
C35, C37, C48, C50, C52: 1n; C0603
C38: 100p; C0402
C39: 47p; C0402
C40: 0p8; C0402
C41: 1p5; C0402
C42, C44: NA; C0402
C43: 0p6; C0402
C45: 1u; C0603
C46, C53: 10n; C0603
C54, C55: 10u; C0603
IC9: SKY66112; SMCM-22
IC10: SX1280; QFN24L
IC11: LP5907MFX-3.3; SOT23-5L
L5, L6, L7: 120R; L0603
LED3: gr; CHIP-LED0603
Q2: FL520WFMT1; CRYSTAL-7M
R6: 3n; R0402
R7: 2n7; R0402
R8: 3n9; R0402
R9: 1k; R0603
RN9, RN10, RN11: 100; EXB28V

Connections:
+5V: L7.2; also elsewhere on the board
CPS: IC9.15 (CPS), RN11.5 (2)
CRX: IC9.2 (CRX), RN11.7 (2)
CTX: IC9.17 (CTX), RN11.8 (2)
GND: ANT.GND1 (GND), ANT.GND2 (GND), ANT.GND3 (GND), ANT.GND4 (GND), C34.2, C35.2, C36.2, C37.2, C40.2, C41.2, C42.2, C43.2, C44.2, C45.2, C46.2, C47.2, C48.2, C49.2, C50.2, C51.2, C52.2, C53.2, C54.2, C55.2, IC9.1 (GND), IC9.4 (ANT_SEL), IC9.5 (GND), IC9.7 (GND), IC9.9 (GND), IC9.10 (GND), IC9.12 (GND), IC9.13 (GND), IC9.18 (GND), IC9.20 (GND), IC9.22 (GND), IC9.PAD1 (GND), IC9.PAD2 (GND), IC10.5 (GND), IC10.13 (GND), IC10.20 (GND), IC10.21 (GND), IC10.23 (GND), IC10.24 (GND), IC10.PAD (GND), IC11.2 (GND), LED3.C, Q2.2 (GND1), Q2.4 (GND1), RN10.2 (1), RN10.3 (1), RN10.6 (2), RN10.7 (2); also elsewhere on the board
unnamed: LED3.A, R9.1
unnamed: C54.1, IC11.1 (VIN), L7.1
unnamed: IC10.17 (MOSI), RN9.8 (2)
unnamed: IC10.16 (MISO), RN9.7 (2)
unnamed: IC10.18 (SCK), RN9.6 (2)
unnamed: IC10.19 (!CS), RN9.5 (2)
unnamed: IC10.7 (BUSY), RN10.5 (2)
unnamed: IC10.8 (DIO1), RN10.8 (2)
unnamed: IC10.4 (XTB), Q2.3 (2)
unnamed: IC10.6 (XTA), Q2.1
unnamed: C45.1, C46.1, IC10.2 (VDD_IN), IC10.12 (DCC_FB)
unnamed: C53.1, IC10.1 (VR_PA)
unnamed: C38.2, IC9.21 (RFIN)
unnamed: C33.1, C41.1, R6.2, R7.1
unnamed: C33.2, C38.1, C42.1, R7.2
unnamed: C40.1, IC10.22 (RFIO), R6.1
unnamed: C39.1, IC9.8 (ANT1)
unnamed: C39.2, C43.1, R8.1
unnamed: ANT.C (1), C44.1, R8.2
SPI1-MISO: RN9.2 (1); also elsewhere on the board
SPI1-MOSI: RN9.1; also elsewhere on the board
SPI1-SCK: RN9.3 (1); also elsewhere on the board
WF-3V3: C55.1, IC11.5 (VOUT), L5.1, L6.1, R9.2
WF-BUSY: RN10.4 (1); also elsewhere on the board
WF-CPS: RN11.4 (1); also elsewhere on the board
WF-CRX: RN11.2 (1); also elsewhere on the board
WF-CS: RN9.4 (1); also elsewhere on the board
WF-CTX: RN11.1; also elsewhere on the board
WF-IRQ: RN10.1; also elsewhere on the board
WF-ON: IC11.3 (ON); also elsewhere on the board
WF_3V3FEM: C47.1, C48.1, C49.1, C50.1, C51.1, C52.1, IC9.3 (CSD), IC9.11 (VDD), IC9.14 (VCC2), IC9.16 (VCC1), IC9.19 (CHL), L6.2
WF_3V3SX: C34.1, C35.1, C36.1, C37.1, IC10.3 (!RESET), IC10.11 (V_DIO), IC10.15 (VBAT), L5.2

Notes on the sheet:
Design: A. Ryll
Wireless Interface


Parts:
C56, C58: 33u; C1206; VOLTAGE 25V
C57, C59: 100n; C0603
IC12: LT3080ST; SOT223
IDD: TE-FPC-1MM-8V; TE-1734248-8
L8: 470R; L1206
LED4: gr; CHIP-LED0603
LEDS: TE-FPC-1MM-10H; TE-1-84952-0
PAD1, PAD2, PAD3: WIREPAD5,4/3,0; 5,4/3,0
PWR: 4-1734742-0; TE-4-1734592-0
R10: 1k; R0603
R11: 330k; R0603
SW2: KT11P4SA3M; KT11
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

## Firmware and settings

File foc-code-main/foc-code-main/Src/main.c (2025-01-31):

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
/* Includes ------------------------------------------------------------------*/
#include "main.h"

/* USER CODE BEGIN Includes */
#include <stdio.h>
#include <stdlib.h>
/* USER CODE END Includes */

ADC_HandleTypeDef hadc1;
ADC_HandleTypeDef hadc2;

COMP_HandleTypeDef hcomp1;
COMP_HandleTypeDef hcomp2;
COMP_HandleTypeDef hcomp4;

CORDIC_HandleTypeDef hcordic;

DAC_HandleTypeDef hdac3;

OPAMP_HandleTypeDef hopamp1;
OPAMP_HandleTypeDef hopamp2;
OPAMP_HandleTypeDef hopamp3;

TIM_HandleTypeDef htim1;

UART_HandleTypeDef huart2;
DMA_HandleTypeDef hdma_usart2_rx;

void SystemClock_Config(void);
static void MX_GPIO_Init(void);
static void MX_DMA_Init(void);
static void MX_ADC1_Init(void);
static void MX_ADC2_Init(void);
static void MX_COMP1_Init(void);
static void MX_COMP2_Init(void);
static void MX_COMP4_Init(void);
static void MX_CORDIC_Init(void);
static void MX_DAC3_Init(void);
static void MX_OPAMP1_Init(void);
static void MX_OPAMP2_Init(void);
static void MX_OPAMP3_Init(void);
static void MX_TIM1_Init(void);
static void MX_USART2_UART_Init(void);
static void MX_NVIC_Init(void);
/**
  * @brief  The application entry point.
  * @retval int
  */
int main(void)
{

  /* USER CODE BEGIN 1 */
  uint8_t unsigned_data_buffer[1];
  unsigned_data_buffer[0] = 0;
  int16_t signed_data_buffer = -1;
  int16_t new_speed = signed_data_buffer;
  int16_t old_speed = new_speed;
  uint16_t ramp_duration = 0;
  uint16_t speed_difference = 0;

  int temp = -1;

  const uint16_t amount_of_data = 8;
  const uint32_t timeout_duration = 100000;

  HAL_StatusTypeDef uart_status;

  /* USER CODE END 1 */

  /* MCU Configuration--------------------------------------------------------*/

  /* Reset of all peripherals, Initializes the Flash interface and the Systick. */
  HAL_Init();

  /* Configure the system clock */
  SystemClock_Config();

  /* Initialize all configured peripherals */
  MX_GPIO_Init();
  MX_DMA_Init();
  MX_ADC1_Init();
  MX_ADC2_Init();
  MX_COMP1_Init();
  MX_COMP2_Init();
  MX_COMP4_Init();
  MX_CORDIC_Init();
  MX_DAC3_Init();
  MX_OPAMP1_Init();
  MX_OPAMP2_Init();
  MX_OPAMP3_Init();
  MX_TIM1_Init();
  MX_USART2_UART_Init();
  MX_MotorControl_Init();

  /* Initialize interrupts */
  MX_NVIC_Init();
  /* Infinite loop */
  /* USER CODE BEGIN WHILE */

  /* Initialize motor */
  MC_ProgramSpeedRampMotor1(0, 0);

  while (1)
  {
	  /*
	     * Check continuously for inputs from UART.
	     * If there is a new command it should be implemented straight away.
	     * The information passed should be
	     * A function that checks interrupts
	     * A function that stops the motor
	  */
	  /* Receive speed commands over UART and map them to signed */
	  uart_status = HAL_UART_Receive(&huart2, unsigned_data_buffer, amount_of_data, timeout_duration);
	  if(uart_status == HAL_OK)
	  {
		  temp = (unsigned_data_buffer[0] *(65535/255)) - 32768;
		  signed_data_buffer = (int16_t)temp;
		  /* Ensure only safe and acceptable speed commands are processed */
		  if((signed_data_buffer > -10000) && (signed_data_buffer < 10000))//uart_status == HAL_OK
		  {
			  //HAL_GPIO_WritePin(led_red_GPIO_Port, led_red_Pin, GPIO_PIN_RESET);
			  new_speed = signed_data_buffer;
			  /* Update speed if new value has been provided */
			  if(new_speed != old_speed)
			  {
				  HAL_GPIO_WritePin(led_red_GPIO_Port, led_red_Pin, GPIO_PIN_SET);
				  //HAL_Delay(500);
				  speed_difference = abs(old_speed - new_speed);
				  /* Linear ramp time for small differences */
				  if(speed_difference < 1000)
				  {
					  ramp_duration = speed_difference;
				  }
				  /* Static ramp time for larger differences */
				  else
				  {
					  ramp_duration = 1500;
				  }
				  /* Set new speed and save current speed as old speed */
				  MC_ProgramSpeedRampMotor1(new_speed, ramp_duration);
				  MC_StartMotor1();
				  old_speed = new_speed;
			  }
		  }
		  else if((signed_data_buffer) > 10000 && (signed_data_buffer < 65535))
		  {
			for(uint8_t i = 0; i<2; i++)
			{
				HAL_GPIO_WritePin(led_red_GPIO_Port, led_red_Pin, GPIO_PIN_SET);
				HAL_Delay(500);
				HAL_GPIO_WritePin(led_red_GPIO_Port, led_red_Pin, GPIO_PIN_RESET);
				HAL_Delay(500);
			}
		  }
		  else if((signed_data_buffer > -65535) && (signed_data_buffer < -10000))
		  {
			  for(uint8_t i = 0; i<4; i++)
			  {
				  HAL_GPIO_WritePin(led_red_GPIO_Port, led_red_Pin, GPIO_PIN_SET);
				  HAL_Delay(500);
				  HAL_GPIO_WritePin(led_red_GPIO_Port, led_red_Pin, GPIO_PIN_RESET);
				  HAL_Delay(500);
			  }
		  }
	  }
    /* USER CODE END WHILE */

    /* USER CODE BEGIN 3 */
  }
  /* Stop motor */
  MC_StopMotor1();
  /* USER CODE END 3 */
}

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


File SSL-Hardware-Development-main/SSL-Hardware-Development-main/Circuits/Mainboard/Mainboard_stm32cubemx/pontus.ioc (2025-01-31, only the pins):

Mcu.UserName=STM32H723ZGTx
PA0.GPIO_Label=M1_PWM
PA0.Signal=S_TIM5_CH1
PA1.GPIO_Label=M1_Encoder_B
PA1.Signal=S_TIM2_CH2
PA10.GPIO_Label=USB_FS_ID
PA10.Signal=USB_OTG_HS_ID
PA11.GPIO_Label=USB_FS_DM
PA11.Signal=USB_OTG_HS_DM
PA12.GPIO_Label=USB_FS_DP
PA12.Signal=USB_OTG_HS_DP
PA13(JTMS/SWDIO).GPIO_Label=SWDIO
PA13(JTMS/SWDIO).Signal=DEBUG_JTMS-SWDIO
PA14(JTCK/SWCLK).GPIO_Label=SWCLK
PA14(JTCK/SWCLK).Signal=DEBUG_JTCK-SWCLK
PA15(JTDI).GPIO_Label=M1_Encoder_A
PA15(JTDI).Signal=S_TIM2_CH1_ETR
PA2.GPIO_Label=M2_TX
PA2.Signal=USART2_TX
PA3.GPIO_Label=M2_RX
PA3.Signal=USART2_RX
PA4.GPIO_Label=WSENS_CS
PA4.Signal=GPIO_Output
PA5.GPIO_Label=WSENS_SCL
PA5.Signal=SPI1_SCK
PA6.GPIO_Label=WSENS_SAO
PA6.Signal=SPI1_MISO
PA7.GPIO_Label=RMII_CRS_DV
PA7.Signal=ETH_CRS_DV
PA8.GPIO_Label=VL6180_SCL
PA8.Signal=I2C3_SCL
PA9.GPIO_Label=USB_FS_VBUS
PA9.Signal=USB_OTG_HS_VBUS
PB0.GPIO_Label=LED_GREEN
PB0.Signal=GPIO_Output
PB10.GPIO_Label=VL53L4CD_SCL
PB10.Signal=I2C2_SCL
PB11.GPIO_Label=VL53L4CD_SDA
PB11.Signal=I2C2_SDA
PB12.GPIO_Label=Rpi_RX
PB12.Signal=UART5_RX
PB13.GPIO_Label=RMII_TXD1
PB13.Signal=ETH_TXD1
PB14.GPIO_Label=M5_PWM
PB14.Signal=S_TIM12_CH1
PB15.GPIO_Label=M1_RX
PB15.Signal=USART1_RX
PB3(JTDO/TRACESWO).GPIO_Label=SWO
PB3(JTDO/TRACESWO).Signal=DEBUG_JTDO-SWO
PB4(NJTRST).GPIO_Label=M2_Encoder_A
PB4(NJTRST).Signal=S_TIM3_CH1
PB5.GPIO_Label=M2_Encoder_B
PB5.Signal=S_TIM3_CH2
PB6.GPIO_Label=M1_TX
PB6.Signal=USART1_TX
PB7.GPIO_Label=M3_Encoder_B
PB7.Signal=S_TIM4_CH2
PB8.GPIO_Label=SEN0374_SCL
PB8.Signal=I2C1_SCL
PB9.GPIO_Label=SEN0374_SDA
PB9.Signal=I2C1_SDA
PC1.GPIO_Label=RMII_MDC
PC1.Signal=ETH_MDC
PC10.GPIO_Label=M5_TX
PC10.Signal=UART4_TX
PC11.GPIO_Label=M5_RX
PC11.Signal=UART4_RX
PC12.GPIO_Label=Rpi_TX
PC12.Signal=UART5_TX
PC13.GPIO_Label=B1 (Blue_User_Button)
PC13.Signal=GPIO_Input
PC14-OSC32_IN.Signal=RCC_OSC32_IN
PC15-OSC32_OUT.Signal=RCC_OSC32_OUT
PC2_C.GPIO_Label=RF_MISO
PC2_C.Signal=SPI2_MISO
PC3_C.GPIO_Label=RF_MOSI
PC3_C.Signal=SPI2_MOSI
PC4.GPIO_Label=RMII_RXD0
PC4.Signal=ETH_RXD0
PC5.GPIO_Label=RMII_RXD1
PC5.Signal=ETH_RXD1
PC6.GPIO_Label=M4_Encoder_A
PC6.Signal=S_TIM8_CH1
PC7.GPIO_Label=M4_Encoder_B
PC7.Signal=S_TIM8_CH2
PC8.GPIO_Label=VL6180_IO0
PC8.Signal=GPIO_Output
PC9.GPIO_Label=VL6180_SDA
PC9.Signal=I2C3_SDA
PD10.Signal=GPIO_Output
PD12.GPIO_Label=M3_Encoder_A
PD12.Signal=S_TIM4_CH1
PD13.GPIO_Label=SEN0374_INT
PD13.Signal=GPIO_Output
PD14.GPIO_Label=SEN0374_Boot
PD14.Signal=GPIO_Output
PD15.GPIO_Label=SEN0374_PS1
PD15.Signal=GPIO_Output
PD3.GPIO_Label=RF_SCK
PD3.Signal=SPI2_SCK
PD7.GPIO_Label=WSENS_SDA
PD7.Signal=SPI1_MOSI
PD8.GPIO_Label=STLK_VCP_RX
PD8.Signal=USART3_TX
PD9.GPIO_Label=STLK_VCP_TX
PD9.Signal=USART3_RX
PE1.GPIO_Label=LED_YELLOW
PE1.Signal=GPIO_Output
PE15.GPIO_Label=RF_CS
PE15.Signal=GPIO_Output
PE2.GPIO_Label=M4_RX
PE2.Signal=USART10_RX
PE3.GPIO_Label=M4_TX
PE3.Signal=USART10_TX
PE5.GPIO_Label=M2_PWM
PE5.Signal=S_TIM15_CH1
PF0.GPIO_Label=VL53L4CD2_SDA
PF0.Signal=I2C5_SDA
PF1.GPIO_Label=VL53L4CD2_SCL
PF1.Signal=I2C5_SCL
PF11.GPIO_Label=M4_PWM
PF11.Signal=TIM24_CH1
PF14.GPIO_Label=ADPS-9960_SCL
PF14.Signal=I2C4_SCL
PF15.GPIO_Label=ADPS-9960_SDA
PF15.Signal=I2C4_SDA
PF2.GPIO_Label=VL53L4CD_SHUT
PF2.Signal=GPIO_Output
PF3.GPIO_Label=VL53L4CD_INT
PF3.Signal=GPIO_Output
PF4.GPIO_Label=VL53L4CD2_INT
PF4.Signal=GPIO_Output
PF5.GPIO_Label=VL53L4CD2_SHUT
PF5.Signal=GPIO_Output
PF6.GPIO_Label=M3_PWM
PF6.Signal=TIM23_CH1
PG11.GPIO_Label=RMII_TX_EN
PG11.Signal=ETH_TX_EN
PG13.GPIO_Label=RMII_TXD0
PG13.Signal=ETH_TXD0
PG14.GPIO_Label=M3_TX
PG14.Signal=USART6_TX
PG2.GPIO_Label=SEN0374_PS2
PG2.Signal=GPIO_Output
PG3.GPIO_Label=SEN0374_BL-IND
PG3.Signal=GPIO_Output
PG4.GPIO_Label=SEN0374_RST
PG4.Signal=GPIO_Output
PG5.Signal=GPIO_Output
PG6.GPIO_Label=ADPS-9960_INT
PG6.Signal=GPIO_Output
PG7.GPIO_Label=USB_FS_OVCR
PG7.Signal=GPXTI7
PG8.GPIO_Label=VL6180_IO1
PG8.Signal=GPIO_Output
PG9.GPIO_Label=M3_RX
PG9.Signal=USART6_RX
PH0-OSC_IN.GPIO_Label=MCO
PH0-OSC_IN.Signal=RCC_OSC_IN
PH1-OSC_OUT.Signal=RCC_OSC_OUT

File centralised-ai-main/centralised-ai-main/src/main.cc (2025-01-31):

/* main.cc
 *==============================================================================
 * Author: Jacob Johansson, Emil Åberg, Viktor Eriksson
 * Creation date: 2024-09-16
 * Last modified: 2024-12-12 by Jacob Johansson & Viktor Eriksson
 * Description: Main function.
 * License: See LICENSE file for license details.
 *==============================================================================
 */

/* C++ standard library */
#include "vector"

/* Project .h files */
#include "collective-robot-behaviour/mappo.h"
#include "collective-robot-behaviour/network.h"
#include "collective-robot-behaviour/utils.h"
#include "simulation-interface/simulation_interface.h"
#include "ssl-interface/ssl_vision_client.h"

#include "collective-robot-behaviour/communication.h"
#include "collective-robot-behaviour/evaluation.h"
#include "common_types.h"

#include "common_types.h"
#include "ctime"
#include "iostream"
#include "matplotlibcpp.h"
#include "pybind11/embed.h"
#include "pybind11/stl.h"

int main() {
  /* Create the centralised critic network class */
  centralised_ai::collective_robot_behaviour::CriticNetwork critic;
  // centralised_ai::collective_robot_behaviour::PolicyNetwork policy;

  /* Comment out if want to create new agents, otherwise load in saved models*/
  centralised_ai::collective_robot_behaviour::PolicyNetwork policy =
      centralised_ai::collective_robot_behaviour::CreatePolicy();
  // LoadNetworks(policy, critic);

  /* Define the IP and port for the VisionClient */
  std::string vision_ip = "127.0.0.1";
  int vision_port = 10006;

  /* Define the IP and command listen port for grSim */
  std::string grsim_ip = "127.0.0.1";
  int grsim_port = 20011;

  /* Create the VisionClient instance with IP and port */
  centralised_ai::ssl_interface::VisionClient vision_client(vision_ip,
                                                            vision_port);
  vision_client.ReceivePacketsUntilAllDataRead();

  /* Create the AutomatedReferee instance with the VisionClient */
  centralised_ai::ssl_interface::AutomatedReferee referee(vision_client,
                                                          grsim_ip, grsim_port);

  /* Start the automated referee */
  referee.StartGame(centralised_ai::Team::kBlue, centralised_ai::Team::kYellow,
                    3.0F, 300);

  std::vector<centralised_ai::simulation_interface::SimulationInterface>
      simulation_interfaces;
  for (int32_t id = 0; id < centralised_ai::amount_of_players_in_team; id++) {
    simulation_interfaces.push_back(
        centralised_ai::simulation_interface::SimulationInterface(
            grsim_ip, grsim_port, id, centralised_ai::Team::kBlue));
  }

  /* Generate the file name from date. */
  /* Get current time */
  auto now = std::chrono::system_clock::now();
  std::time_t now_time = std::chrono::system_clock::to_time_t(now);

  /* Convert to local time and format */
  std::tm local_time = *std::localtime(&now_time);
  std::ostringstream oss;
  oss << std::put_time(&local_time,
                       "%Y-%m-%d_%H-%M-%S"); // e.g., "2024-09-12_14-30-00"

  /* Create the file name */
  std::string reward_file_name = "../rewards/reward_" + oss.str() + ".csv";
  std::string losses_file_name = "../losses/losses_" + oss.str() + ".csv";
  std::cout << "File name to save rewards: " << reward_file_name << std::endl;
  std::cout << "File name to save losses: " << losses_file_name << std::endl;

  /* Save the initial state of the networks. */
  centralised_ai::collective_robot_behaviour::SaveOldNetworks(policy, critic);

  int epochs = 0;
  std::cout << "Running" << std::endl;
  while (true) {
    referee.StartGame(centralised_ai::Team::kBlue,
                      centralised_ai::Team::kYellow, 3.0F, 300);
    /*run actions and save  to buffer*/
    auto databuffer = centralised_ai::collective_robot_behaviour::MappoRun(
        policy, critic, referee, vision_client, centralised_ai::Team::kBlue,
        simulation_interfaces);

    /*Run Mappo Agent algorithm by Policy Models and critic network*/
    torch::Tensor losses =
        centralised_ai::collective_robot_behaviour::MappoUpdate(policy, critic,
                                                                databuffer);

    /*Save the reward to go to a file*/
    int32_t num_batches = databuffer.size();
    int32_t num_time_steps = databuffer[0].t.size();
    torch::Tensor rewards = torch::zeros({num_batches, num_time_steps});

    for (int32_t b = 0; b < databuffer.size(); b++) {
      for (int32_t t = 0; t < databuffer[b].t.size(); t++) {
        rewards[b][t] = databuffer[b].t[t].rewards.mean();
      }
    }

    centralised_ai::collective_robot_behaviour::SaveRewardToFile(
        rewards.mean(), epochs, reward_file_name);

    /* Save the losses to a file */
    centralised_ai::collective_robot_behaviour::SaveLossesToFile(
        losses, losses_file_name);

    /* Update the epoch index */
    std::cout << "* Epochs: " << epochs << std::endl;
    epochs++;
  }

  return 0;
}

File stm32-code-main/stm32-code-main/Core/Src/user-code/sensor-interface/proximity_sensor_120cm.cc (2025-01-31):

/* proximity_sensor_120cm.cc
 *==============================================================================
 * Author: Emil Åberg
 * Creation date: 2024-11-11
 * Last modified: 2024-11-20 by Emil Åberg
 * Description: Driver for the VL53L4CD 120cm proximity sensor. This driver
 * functions as a wrapper for ST's Ultra Lite Driver which can be found
 * here: https://www.st.com/en/embedded-software/stsw-img026.html
 * License: See LICENSE file for license details.
 *==============================================================================
 */

/* Related .h file */
#include "../../user-code/sensor-interface/proximity_sensor_120cm.h"

/* Project .h files */
#include "stm32h7xx_hal.h"
#include "../../user-code/common_types.h"
#include "../../../Drivers/VL53L4CD_ULD_Driver/VL53L4CD_api.h"

namespace stm32_code
{
namespace sensor_interface
{

/* Default constructor */
ProximitySensor120cm::ProximitySensor120cm() {}

/* Configure the sensor to begin taking measurements */
Status ProximitySensor120cm::Init(I2C_HandleTypeDef* i2c_handle)
{
  VL53L4CD_Error status;
  i2c_handle_ = i2c_handle;
  status = VL53L4CD_SensorInit(i2c_handle, kI2cAddress_);

  if (status == 0)
  {
    status = VL53L4CD_StartRanging(i2c_handle, kI2cAddress_);
  }

  if (status == 0)
  {
    return Status::kOk;
  }
  else
  {
	  return Status::kNotOk;
  }
}

/* Returns the measured distance in mm */
Scalar<uint16_t> ProximitySensor120cm::GetDistance()
{
  uint8_t data_ready;
  VL53L4CD_ResultsData_t result;
  Scalar<uint16_t> distance;

  VL53L4CD_CheckForDataReady(i2c_handle_, kI2cAddress_, &data_ready);

  if (data_ready == 1)
  {
    VL53L4CD_GetResult(i2c_handle_, kI2cAddress_, &result);
    VL53L4CD_ClearInterrupt(i2c_handle_, kI2cAddress_);
    distance.value = result.distance_mm;

    if (result.range_status == 0)
    {
      distance.status = Status::kOk;
    }
    else
    {
      distance.status = Status::kNotOk;
    }
  }
  else
  {
    distance.status;
  }

  return distance;
}

} /* namespace sensor_interface */
} /* namespace stm32_code */

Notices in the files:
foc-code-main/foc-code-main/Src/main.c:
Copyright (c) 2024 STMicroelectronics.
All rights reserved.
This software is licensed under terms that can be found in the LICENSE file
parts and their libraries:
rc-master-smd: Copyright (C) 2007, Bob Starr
